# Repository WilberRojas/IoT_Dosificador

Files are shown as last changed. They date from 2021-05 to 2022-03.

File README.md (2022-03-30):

# Dosificador de medicamentos inteligente
Puede revisar el articulo en [Articulo.pdf](https://github.com/WilberRojas/IoT_Dosificador/blob/main/Articulo.pdf)

## 1. Comunicación IoT

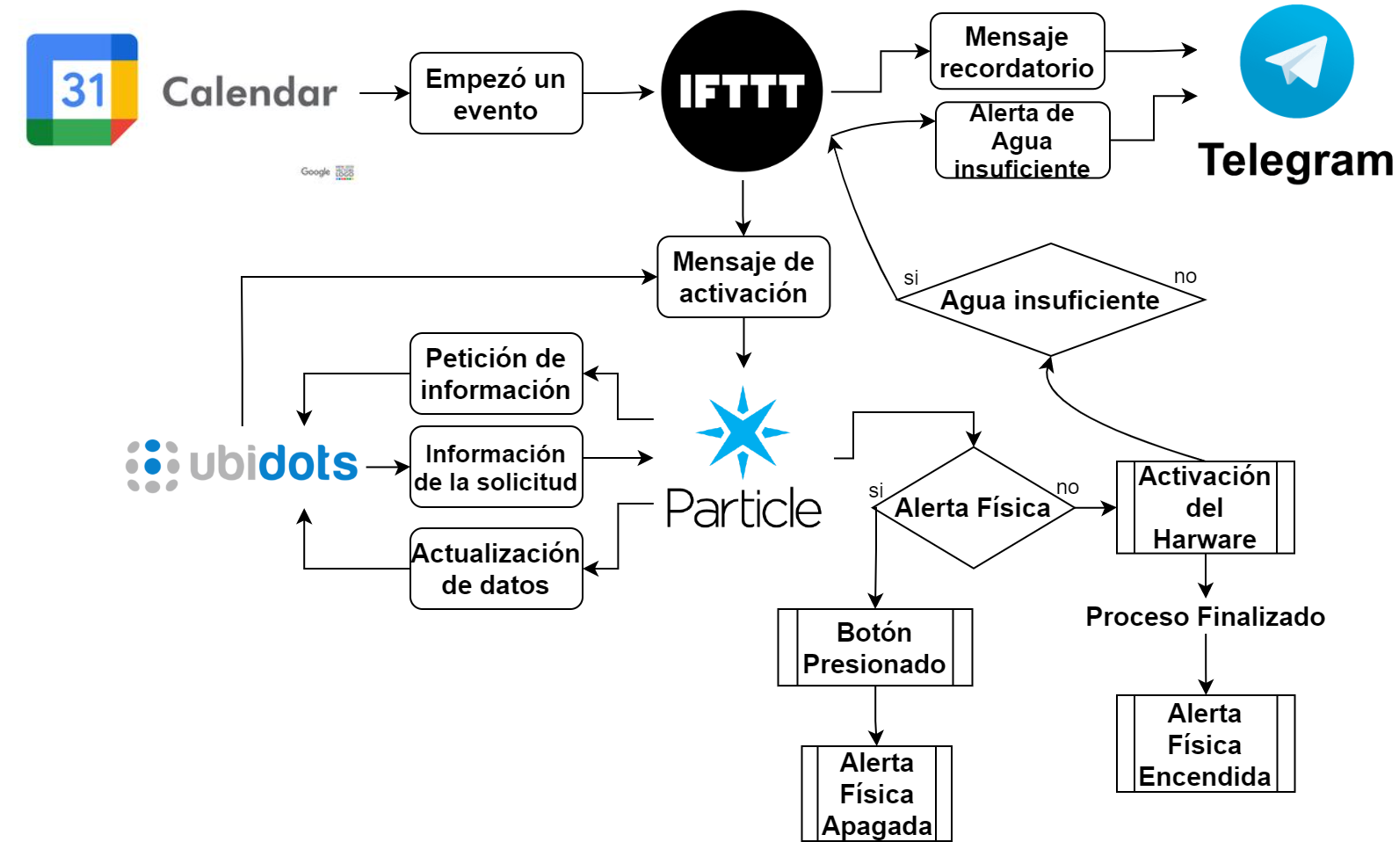
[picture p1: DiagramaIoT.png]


## 2. Prototipo en SolidWorks:

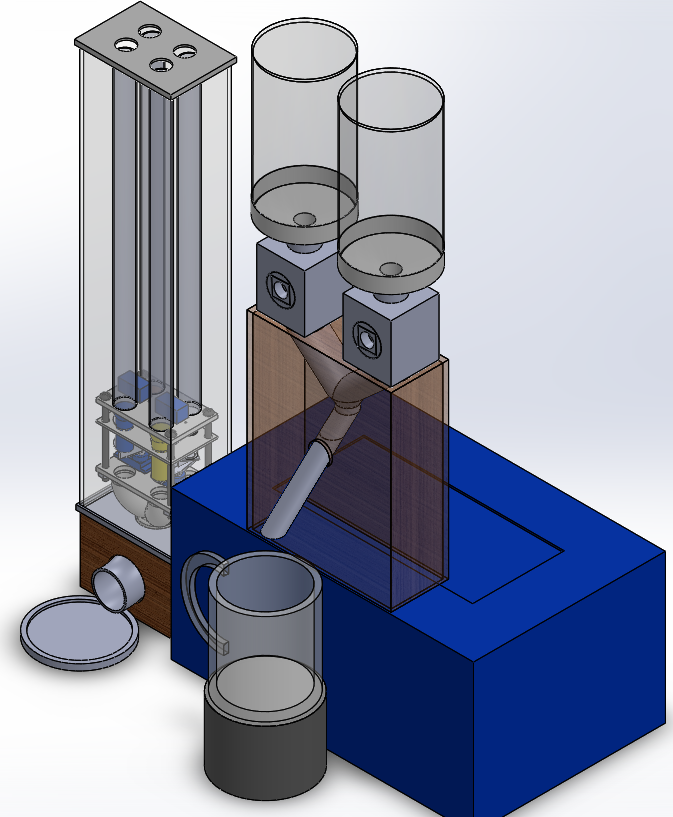
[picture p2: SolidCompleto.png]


Cada pastilla necesita un diseño personalizado en los tubos del mecanismo del dispensador

### 2.1. Mecanismo de las Pastillas

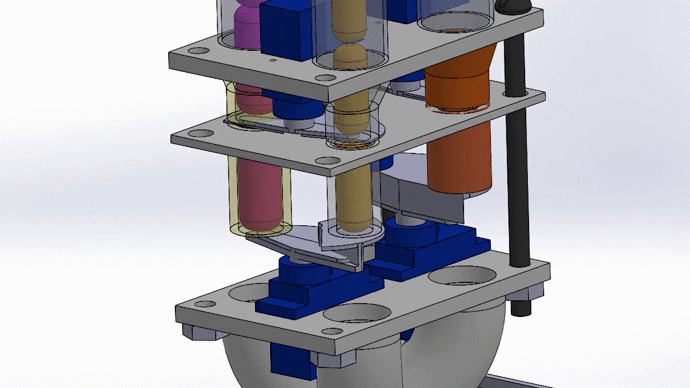
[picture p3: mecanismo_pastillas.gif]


### 2.2. Mecanismo del Azucar

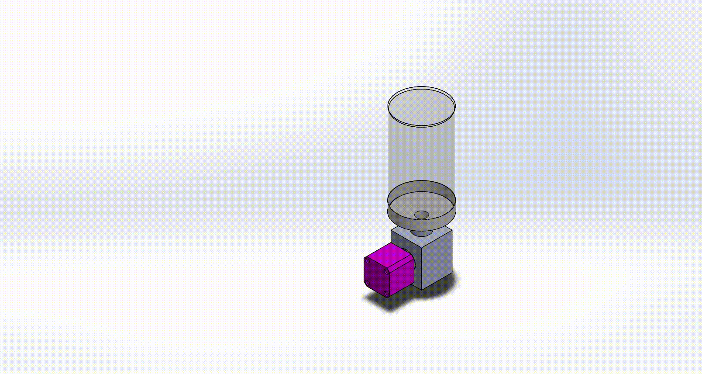
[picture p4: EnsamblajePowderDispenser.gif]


## 3. Diagrama del circuito:

Para diagramar el circuito del proyecto se uso la herramienta de https://fritzing.org/ 

Puede descargar el archivo .fzz aqui: [Diagrama_electronico.fzz](https://github.com/WilberRojas/IoT_Dosificador/blob/main/Diagrama_electronico.fzz?raw=true)

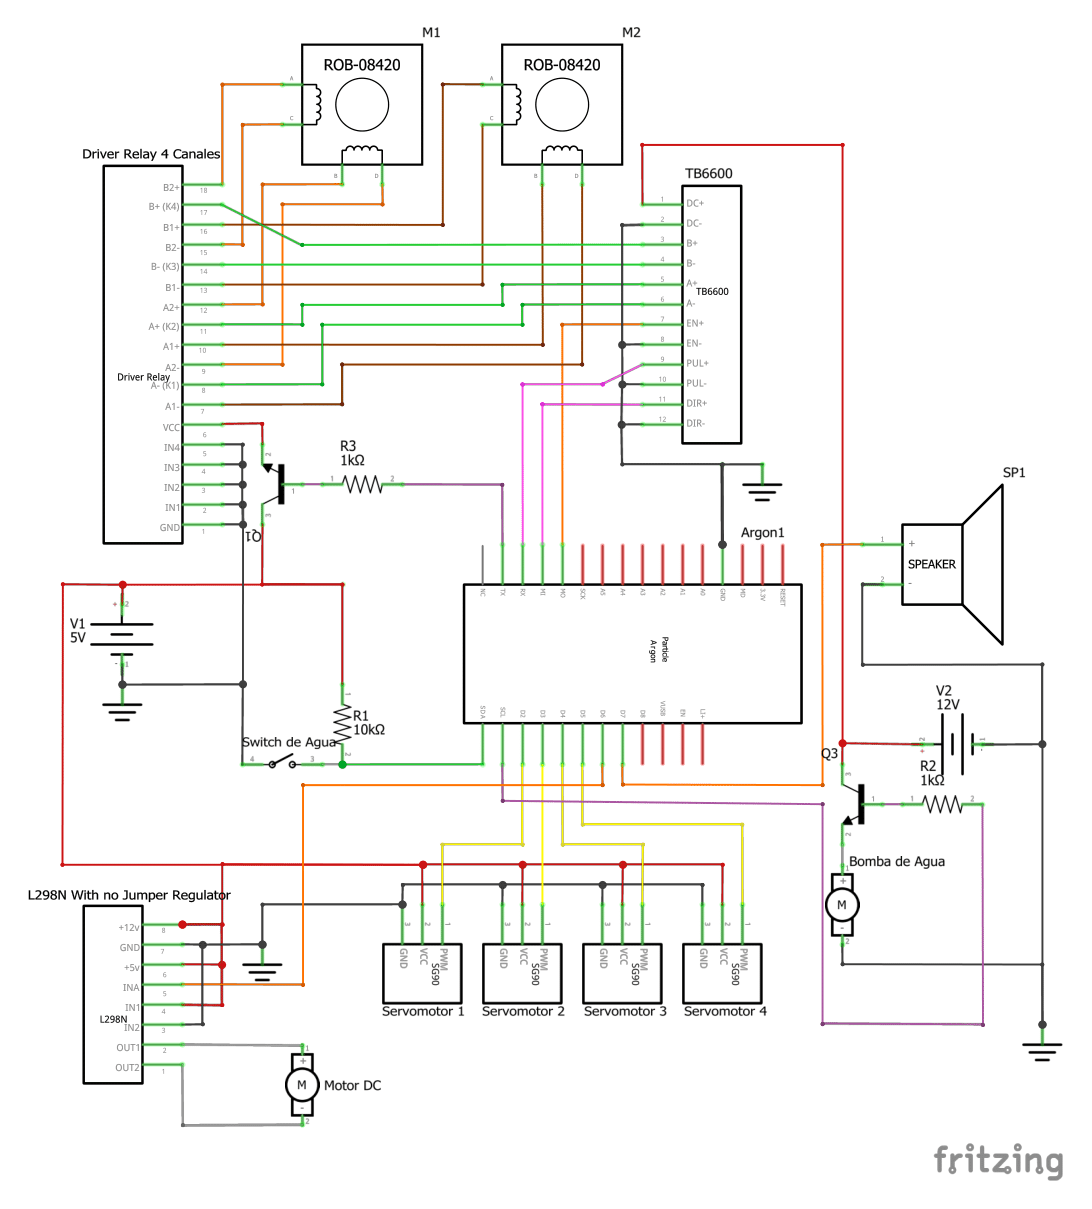
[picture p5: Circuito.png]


NOTA: Es necesario el uso de dos fuentes de alimentacion DC, no es posible alimentar el circuito solo con el VCC de salida la placa Argon debido al uso de multiples motores que requieren gran amperaje.

## 4. Codigo

#### Carpeta ```/src```:
Esta es la carpeta de origen que contiene los archivos de firmware para el proyecto. Todo lo que esté en esta carpeta se compilará en un binario de firmware para el dispositivo Particle.

#### Archivo ```.ino```:
Este archivo es el firmware que se ejecutará como la aplicación principal en el dispositivo Particle. Contiene una función `setup ()` y `loop ()`, y se puede escribir en Wiring o C / C ++. En caso de replica solo de deberá copiar el contenido de este archivo e importar las librerias dentro. Puede revisar el codigo en [stepperL298N.ino](https://github.com/WilberRojas/IoT_Dosificador/blob/main/src/stepperL298N.ino).

#### Archivo ```project.properties```:
Este es el archivo que especifica el nombre y el número de versión de las bibliotecas de las que depende el proyecto. Las dependencias se agregan automáticamente al archivo `project.properties` cuando agrega una biblioteca a un proyecto usando el comando `Particle: Install Library` en el IDE de escritorio.

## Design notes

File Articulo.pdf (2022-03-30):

# Dosificador de medicamentos inteligente

Documento para optar por el Título de Diplomado en Internet of Things Universidad Catolica Boliviana “San Pablo” Regional La Paz ´

Wilber Alvaro Rojas Fern ´ | andez ´
Estudiante del Diplomado en Internet of Things

Fabio Richard Díaz Palacios Coordinador del Diplomado en internet of Things

Resumen—Un gran numero de personas incumplen involunta- ´ riamente las dosis de su medicacion, debido a descuidos humanos. ´ Esto muchas veces repercute en la efectividad del tratamiento y recuperacion. El presente proyecto tiene como objetivo desarro- ´ llar un dispositivo dosificador inteligente para incrementar el cumplimiento de los tratamientos medicos en base a pastillas. ´ El dispositivo hace uso de Google Calendar y Ubidots para la
programacion del consumo, tambi ´ | en incluye un monitoreo de los ´
suministros, como la cantidad de pastillas o agua. El sistema propuesto se comunica con 5 servicios de internet, entre los cuales, implemento los recordatorios por Telegram. El prototipo ´ físico cuenta con la capacidad de almacenar 4 tipos de pastillas y 2 suministros solubles en agua de características arenosas o en
polvo, como el azucar. Para la explicaci ´ | on del prototipo f ´ | ísico,
se desarrollo un prototipo en Solidworks y un diagrama de ´ las conexiones del circuito. Todos los mecanismos desarrollados fueron implementados mediante el uso de la impresion 3D. Las ´ pruebas en el prototipo funcional muestran una variacion a la ´
hora de la activacion programada, retras ´ | andose hasta 10 minutos ´
de la hora exacta. Sin mas complicaciones, se concluy ´ | o que ´
el dispositivo es eficaz para ayudar en el cumplimiento de la dosificacion de pastillas. ´

Palabras clave—Dispensador, Dosificador, Medicacion, IoT, ´ Ubidots, Particle.

Línea de investigacion: ´ Ciencia, Tecnología e Innovacion, ´ Tecnologías de asistencia; desarrollo de dispositivos inteligentes aplicado a la asistencia de personas con discapacidad motora, sensorial, cognitiva.

I. INTRODUCCION´
Seguir las prescripciones de medicacion es importante ´ para obtener resultados positivos en un tratamiento. De manera mas formal, se puede referir al cumplimiento de ´ las prescripciones como la adherencia a la medicacion. La ´ falta de adherencia a la medicacion se asocia con resultados ´ adversos y mayores costos de recuperacion. No obstante, la ´ no adherencia a los medicamentos puede ser intencionada o no. El incumplimiento involuntario es un proceso en el que el paciente puede ser descuidado en el transcurso de completar el tratamiento.

La mayoría de las desviaciones en la toma de medicamentos se deben a omisiones o retrasos en la toma de dosis. Ademas, ´

Este trabajo fue entregado para su revision en fecha 21 de Mayo de ´ 2021. El autor declara que el trabajo es de su completa autoría y referencia adecuadamente otros trabajos.

los tratamientos que requieren terapia a largo plazo se han asociado con la falta de adherencia. Tambien existen otros ´ factores relacionados como la edad joven y la depresion [1]. ´

Vrijens et al. realizaron un estudio, en donde, aproximadamente la mitad de los pacientes a los que se les recetó un medicamento a largo plazo habían dejado de tomarlo en
un ano [2]. Asimismo, la mayor ˜ | ía de los pacientes tenía al
menos un período de “vacaciones de medicamentos”, esto quiere decir que hubo una falta en el cumplimiento de la
medicacion de por lo menos 3 d ´ | ías seguidos. En la imagen
1, se muestra la disminucion a lo largo del tiempo desde el ´ inicio del tratamiento, y se observa que para el día 200 el 35 % de los pacientes ya habían interrumpido el protocolo.

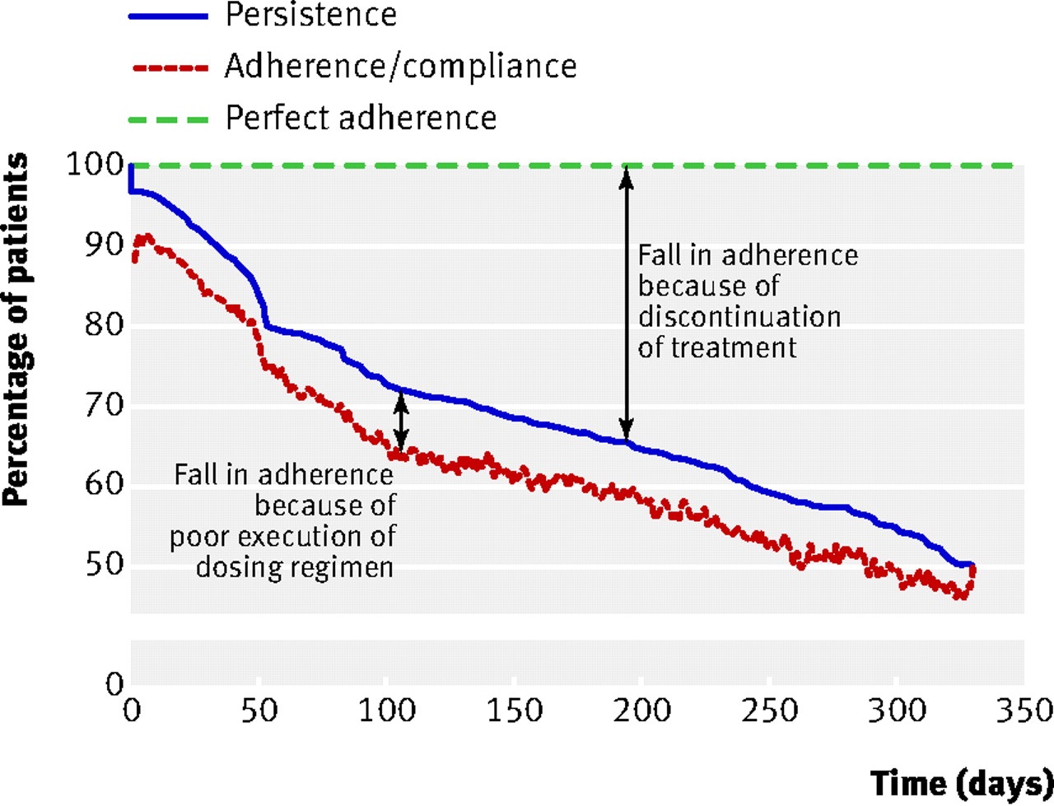
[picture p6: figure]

Figura 1. Seguimiento de la dosificacion en el transcurso de un a ´ | no [2]. ˜

Aproximadamente el 95 % de los pacientes omitieron una dosis en su tratamiento de un ano [2], es decir, tuvieron un ˜
intervalo de mas de 30 horas desde la ´ | ultima dosis tomada. De ´
acuerdo con Vrijens, la efectividad de ejecucion, repercute en ´ la efectividad de persistencia. Se puede hacer enfasis entonces, ´ en la importancia de recordar los horarios de medicacion´ para incrementar la calidad del tratamiento, por lo que en ´ este proyecto, se desarrollara un dispositivo IoT que pueda ´ ser implementado para ayudar en el cumplimiento de la
medicacion por p ´ | íldoras.

II. OBJETIVOS

A. Objetivo General
Desarrollar un dispositivo dosificador inteligente para incrementar el cumplimiento de los tratamientos medicos en base ´ a pastillas.
B. Objetivos Específicos
Implementar un sistema de control IoT.
Disenar un mecanismo capaz de dispensar m ˜ | ultiples ´
píldoras automaticamente. ´
Implementar una programacion para el horario de con- ´ sumo.
Disenar un mecanismo que otorgue complementos para ˜ el consumo bebible.
Implementar un sistema de notificacion y monitoreo. ´

III. RESULTADOS

A. Materiales
Los materiales electronicos utilizados en este proyecto se ´
los listo en la tabla I. Aparte de los listados, tambi ´ | en se us ´ | ó
la impresion 3D para la materializaci ´ | on de los mecanismos ´
disenados. ˜

Tabla I
COMPONENTES ELECTRONICOS ´
Componente | Cantidad
Particle Argon | 1
Motor DC 755 | 1
Servomotor SG90 | 4
Motor Nema 17 | 2
Bomba de agua
AD20P-1230A | 1
Driver L298N | 1
Driver TB6600 | 1
Driver Relay 4 Canales | 1
Sensor de Nivel de Agua ZPC5 | 1
Buzzer Pasivo 5v | 1
Transistor 2n2222 | 2
Resistencia 1K | 2
Resistencia 10K | 1
Fuente de 5v | 1
Fuente de 12v | 1
B. Circuito
Un diagrama completo del circuito del proyecto se puede
encontrar en el Apendice 1. En esta secci ´ | on se explicar ´ | an´
algunos puntos importantes que se tuvo en cuenta en el desarrollo.

Se implementaron 8 motores en total, por lo que se usó fuentes de voltaje externas. Se investigo la corriente necesaria ´ para el funcionamiento de los componentes, como se puede ver en la tabla II, y se calculo el amperaje requerido para ´ ambas fuentes de voltaje. Se obtuvo que la corriente necesaria para la fuente de 5v es 4.88A y para la fuente de 12v es de 4.4A.

Tabla II
AMPERAJE DE LOS COMPONENTES
Componente | Cantidad | Amperaje
Fuente de 5 voltios
Servomotor SG90 | 4 | 200mA
L298N | 1 | 4A
Driver Relay | 1 | 80mA
Fuente de 12 voltios
AD20P-1230A | 1 | 400mA
TB6600 | 1 | 4A
En el calculo, se analiz ´ | o que los dos motores Nema17 que ´
se usaron para el mecanismo del dispensador de azucar y caf ´ | é
del punto C-II, no tienen la necesidad de funcionar al mismo tiempo. Es por eso que se ha implementado un driver de reles´
de 4 canales, el cual cambiar ´ | a las salidas A+, A-, B+ y B- del ´
driver TB6600. Esto incrementa la corriente necesaria de la primera fuente 80mA, pero al usar un driver para dos motores, disminuye la corriente requerida en la segunda fuente 4A. Por otra parte, se implemento transistores como switchs ´ para la activacion de algunos componentes. En la primera ´
version del circuito, se plante ´ | o esta funci ´ | on de activaci ´ | on´
mediante el uso de reles, sin embargo, la corriente necesaria ´ para el accionamiento de un rele de 3v supera a lo que los ´ pines digitales de la placa Argon pueden otorgar. Finalmente, tomando en cuenta los datos de la tabla II , y que la corriente de funcionamiento de la Placa Argon es de 500mA a 5v, la potencia requerida para el funcionamiento del dispositivo es de:
| P = V ∗ I | | (1)

P = 5V ∗ (4,88A + 0,5A) + 12V ∗ 4,4A

| P = 79,7[W]
Se podría calcular tambien el consumo energ ´ | etico diario del ´
dispositivo, suponiendo que este encendido las 24 horas.
| E = P ∗ t | | (2)

E =

79,7 ∗ 24
1000

= 1,91[kW h]

C. Mecanismos
Se desarrollaron dos mecanismos para este proyecto: el
dispensador de pastillas, y el dispensador de azucar y caf ´ | e.´
Para su desarrollo en este proyecto, tambien se elaboraron ´ los mecanismos en Solidworks. Finalmente, se puede hacer una revision del prototipo real en el Anexo 3. ´

C-I. Dispensador de pastillas: La idea del mecanismo del dispensador de pastillas se obtuvo del proyecto de Gursimran [3]. Se usa dos servomotores para controlar la salida de las pastillas, como se observa en la figura 2. A pesar de la simplicidad de este mecanismo, se ha concluido que es uno de
los mas eficientes al momento de automatizar la dosificaci ´ | | | on. ´
Las alternativas a esta solucion implementan una rosca ´ dividida en secciones [4]. El problema con la solucion´ alternativa es que su almacenamiento es mas limitado, por ´

lo que tiene ser recargado con mas frecuencia. Adem ´ | as, ´
su organizacion se basa en el horario del consumo de las ´ pastillas, al contrario del dispensador disenado, en donde la ˜ organizacion se basa en el tipo de pastilla, sin importar el ´ horario. Finalmente, para evitar utilizar una gran cantidad de salidas PWM de la placa Argon, se disenõ un mecanismo que ´ utiliza los mismos dos servomotores para controlar la salida de 2 pastillas, esto se puede observar en el Apendice 2. ´

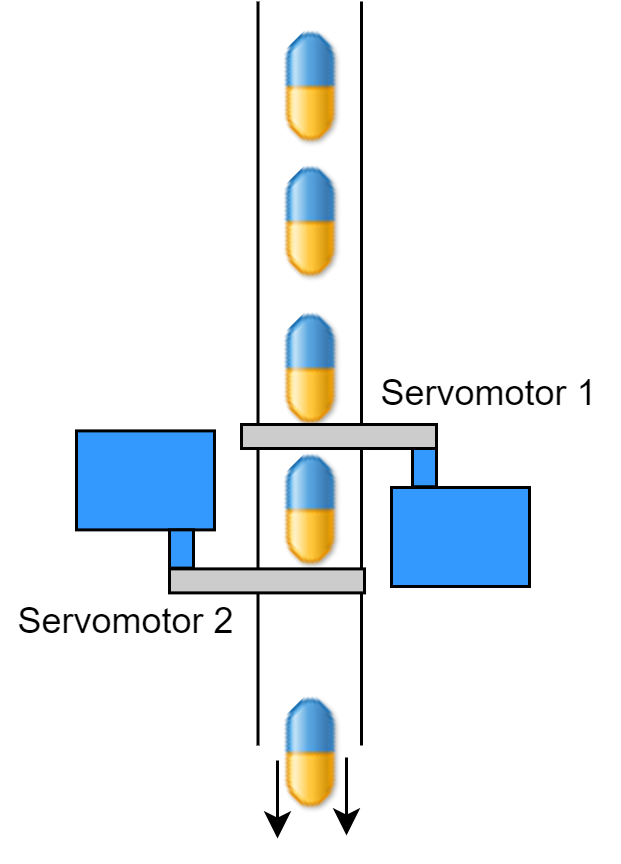
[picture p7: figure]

Figura 2. Esquema del mecanismo dispensador de pastillas.

C-II. Dispensador de azucar y caf ´ | e:´ | La base para el
diseno del dispensador de az ˜ | ucar se obtuvo de la empresa ´
de Polonia “Kazak” [5]. Se lo modifico para que su ac- ´
cionamiento sea electronico, mediante la implementaci ´ | | on de ´
un motor a pasos. Para adicionar un suministro de cafe se ´
disenõ una uni ´ | on por medio de tubos en la salida de estos ´
mecanismos, esto se puede observar mejor en el Apendice 2. ´ El funcionamiento completo de esta implementacion hace uso ´ del AD20P-1230A para adicionar agua al vaso del usuario, para luego ser mesclado por medio del batidor magnetico ´ accionado por el motor DC. La referencia para el diseno del ˜ batidor magnetico se obtuvo de Instructables [6]. ´

IV. IMPLEMENTACION´ IOT

El sistema IoT del proyecto se compone de una conexion en- ´ tre 5 servicios: Ubidots, Particle, IFTTT, Calendar y Telegram.
Se explicara la implementaci ´ | on en cada uno de estos servicios ´
en los siguientes puntos. Un diagrama de esta implementacion´ se puede ver en el apendice 1.
A. Ubidots
El servicio Ubidots permite ser usado como base de datos para las variables del sistema, almacena la informacion´
historicamente y genera una gr ´ | afica independiende para cada ´
variable, como se ve en la figura 3. Con el uso de la librería
de Particle es posible que la placa Argon almacene y recuper ´ | é
datos de este servicio.
Ubidots permite tambien la creaci ´ | on de Dashboards, en ´
donde se pueden anadir indicadores, tablas, interruptores, ˜

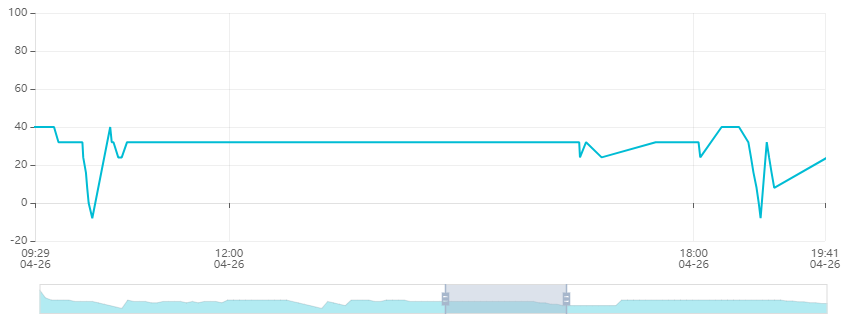
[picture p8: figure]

Figura 3. Grafico de una variable de Ubidots. ´

sliders, etc. Todos los ítems mencionados sirven para interactuar de manera mas sencilla con las variables del ´ sistema. En lo que respecta a este trabajo, los Dashboards
se usaron para hacer una simulacion de una aplicaci ´ | on ideal ´
para el proyecto.
Se dividio la implementaci ´ | on del servicio de Ubidots en ´
dos secciones para la interaccion con el usuario, una secci ´ | on´
de pedido y una seccion de datos. As ´ | í mismo, la seccion de ´
pedido esta compuesta de 3 partes o subsecciones: ´

Subseccion de pastillas ´

En esta subseccion se selecciona qu ´ | e pastillas el usuario ´
quiere tomar mediante el uso de switchs digitales, como se ve en la figura 4.

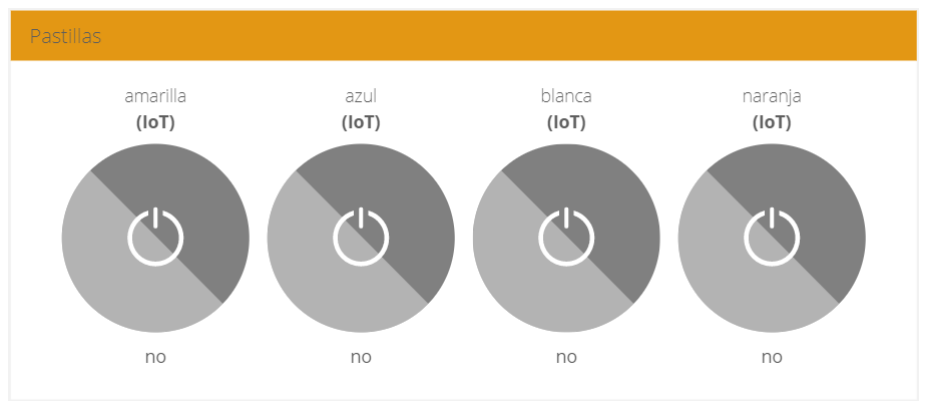
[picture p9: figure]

Figura 4. Seleccion de pastillas. ´

Subseccion de bebidas ´

La primera version implemento switches como en el caso ´ anterior, en donde el usuario podría pedir un valor entre sí o no, sin embargo, esto sería suponer que todos los usuarios consumen sus pastillas con la misma cantidad
de agua, cafe y az ´ | ucar. La implementaci ´ | on de sliders en ´
el dashboard de Ubidots se uso para cambiar el estado de ´ las variables a valores no binarios, permitiendo así una mejor personalizacion en los requerimientos del usuario, ´ como se ve en la figura 5.
Subseccion de envi ´ | ó

Se implemento un switch que al cambiar de estado en ´
sentido RISING mandara una se ´ | nal de activaci ˜ | on al ´
servidor de Particle. Idealmente este componente digital debería ser un boton, sin embargo, Ubidots actualmente ´

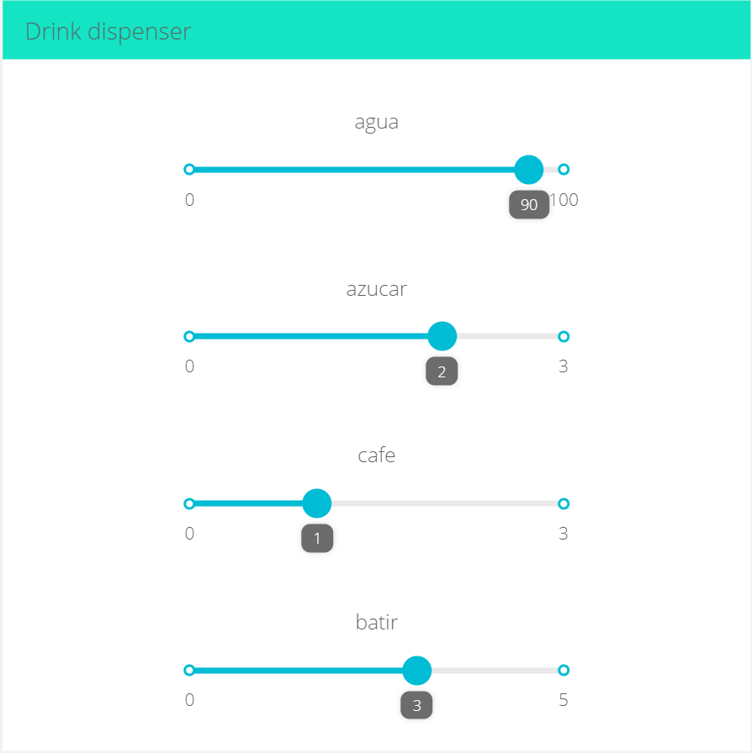
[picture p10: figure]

Figura 5. Seleccion de bebida. ´

no tiene programado un boton para su implementaci ´ | on´
en los Dashboards.
Por otro lado, la seccion de datos est ´ | a compuesta por una ´
tabla que contiene la cantidad y la hora en la que se consumió por ultima vez cada pastilla. ´

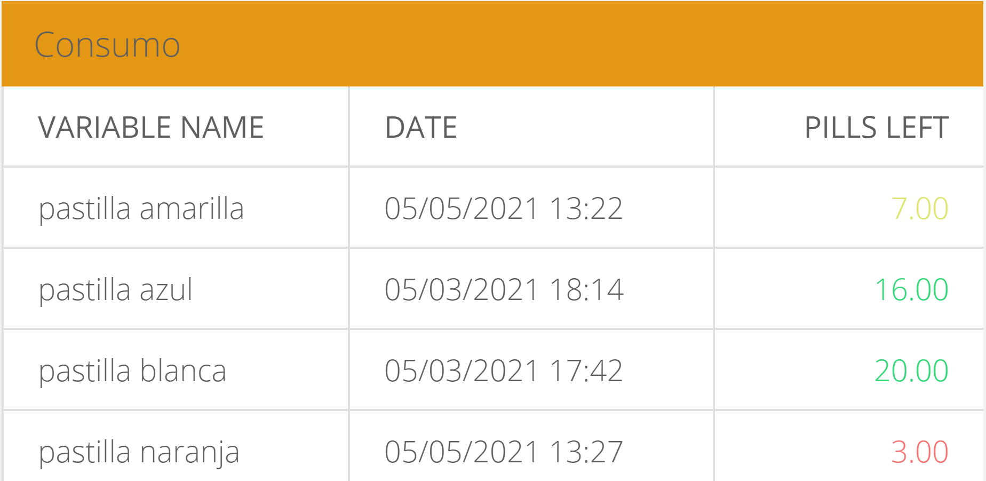
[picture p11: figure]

Figura 6. Consumo de las pastillas.

Ademas, contiene indicadores que muestran el porcentaje ´
de agua, azucar y caf ´ | e que el dispositivo f ´ | ísico almacena en
ese momento.
B. Particle
El servidor de Particle hace posible la interaccion entre ´ servicios IoT y hardware. Recibe los mensajes enviados por Ubidots y IFTTT, como se ve en la figura 7 y 8. Luego de procesar la parte del hardware en base a la solicitud recibida, envía un mensaje a Ubidots para actualizar los datos de la figura 6. Ademas, Ubidots responde si los datos han sido ´ recibidos correctamente.
C. IFTTT, Google Calendar y Telegram
IFTTT es un servicio que permite automatizar la interaccion entre otros servicios de internet. En este proyecto se ´
implemento Google Calendar para la programaci ´ | | on de los ´
horarios en los que se consumira el medicamento. Cuando ´

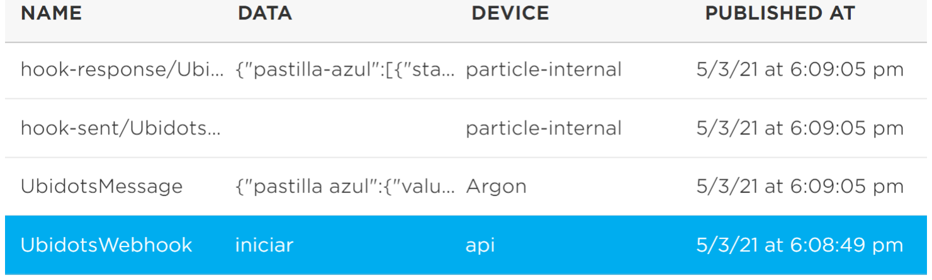
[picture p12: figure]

Figura 7. Mensaje de Inicio de Ubidots.

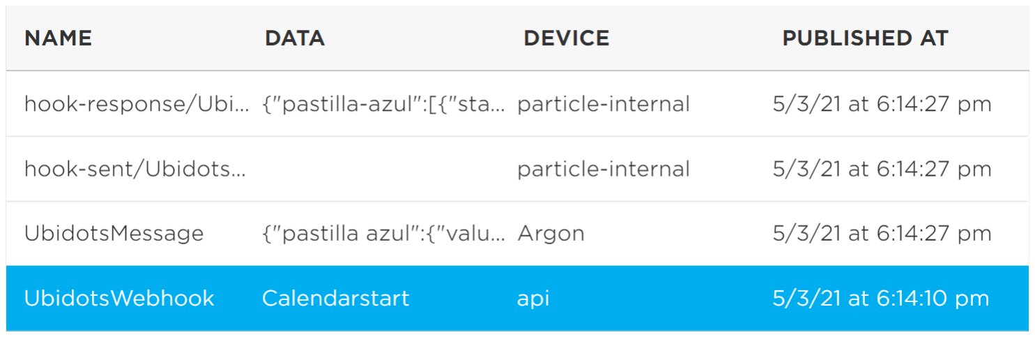
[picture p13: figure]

Figura 8. Mensaje de Inicio de IFTTT.

un evento llamado “pill” inicia, IFTTT manda un mensaje de activacion al servidor de Particle, esto es equivalente a accionar ´ el switch de enviar de la aplicacion de Ubidots. Asimismo, se ´ implemento las notificaciones por Telegram, asegurando que ´ los usuarios reciban un recordatorio a la hora de tomar sus pastillas.

V. RECOMENDACIONES

Para su replicabilidad, en el mecanismo de pastillas se re-
comienda elaborar un diseno personalizado para cada p ˜ | íldora,
debido a que, si el tubo contenedor tiene un diametro interior ´
muy elevado en comparacion al di ´ | ametro de la p ´ | íldora, puede
provocar un atascamiento por un mal asentamiento de las píldoras en cola. Por otro lado, el mecanismo del dispensador
de azucar es replicable para a ´ | nadir m ˜ | as complementos simila- ´
res, para ello se necesitara la implementaci ´ | on de m ´ | as motores a ´
paso, se sugiere utilizar un conjunto de reles para intercambiar ´ la salida del driver controlador, con el objetivo de hacer uso de un solo componente y disminuir el consumo energetico. ´ Finalmente, se recomienda una comunicacion directa entre la ´ placa Argon y Telegram, debido a que el servicio de IFTTT ´ presenta retrasos al momento de activar algunos eventos.

VI. CONCLUSIONES

Se ha desarrollado un dispositivo que cuenta con dos mecanismos principales: El dispensador de pastillas, en donde
su almacenamiento depende del tamano de cada p ˜ | íldora. El
dispensador de azucar y caf ´ | e, que junto con el funcionamiento ´
de la bomba de agua y el batidor magnetico permite una ´ solucion m ´ as completa para los usuarios. Por parte de la ´ implementacion IoT, se ha desarrollado un sistema capaz de ´ solicitar al dispositivo las pastillas y el complemento bebible
por medio de la aplicacion de Ubidots, con la opci ´ | on de ´
programar los pedidos en el servicio de Google Calendar.
Ademas, en el servicio de Ubidots tambi ´ | en se ha desarrollado ´
un monitoreo de las variables mas importantes del sistema. ´

Asimismo, se implemento recordatorios de los eventos pro- ´ gramados a Telegram. Respecto a las pruebas del prototipo funcional, se ha podido notar que para el mecanismo de las pastillas se requiere un diseno personalizado para cada ˜ píldora. Por otra parte, la activacion del sistema por medio ´ de las programaciones en Google Calendar tienden a variar,
adelantandose 2 minutos o retras ´ | andose hasta 10 minutos en ´
las pruebas. Segun la investigaci ´ | on previa, este retraso no es ´
capaz afectar la efectividad de un tratamiento, por lo que se
considera que el prototipo es valido para un desarrollo m ´ | as´
formal.

APENDICES ´

Los siguientes apendices se encuentran en el mismo repo- ´ sitorio de Github, para una mejor revision se ha separado los ´ puntos de interes en los siguientes enlaces: ´
1. Diagrama del circuito:
https://github.com/WilberRojas/IoT Dosificador/blob/ main/Circuito.md (https://github.com/WilberRojas/IoT_Dosificador/blob/main/Circuito.md)
2. Mecanismos:
https://github.com/WilberRojas/IoT Dosificador/blob/ main/mecanismos.md (https://github.com/WilberRojas/IoT_Dosificador/blob/main/mecanismos.md)
3. Prototipo Funcional:
https://github.com/WilberRojas/IoT Dosificador/blob/ main/prototipo.md (https://github.com/WilberRojas/IoT_Dosificador/blob/main/prototipo.md)
4. Codigo desarrollado para la placa Argon: ´ https://github.com/WilberRojas/IoT Dosificador/blob/ main/src/stepperL298N.ino (https://github.com/WilberRojas/IoT_Dosificador/blob/main/src/stepperL298N.ino)

Dashboards de Ubidots:
5. Pedido:
https://industrial.ubidots.com/app/dashboards/public/dashboard/qjiZKvvSNUD0r489xztf1Z11zDqJjdyEKZhmq-uRaM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 (https://industrial.ubidots.com/app/dashboards/public/dashboard/qjiZKvvSN_UD0r489xztf1Z11zDqJjdyEKZhmq-uRaM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)
6. Datos:
https://industrial.ubidots.com/app/dashboards/public/dashboard/F6vTkCbCQBkJ2pRupIU9-EW1M6ufowQUOtWs-vJPUw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 (https://industrial.ubidots.com/app/dashboards/public/dashboard/F6vTkCbCQBkJ2pRupIU9-EW1M6_ufowQUOtWs-vJPUw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)

REFERENCIAS

[1] P. Michael, C. Bryson, and J. S. Rumsfeld, “Medication adherence,” Circulation, vol. 119, 6 2009.
[2] B. Vrijens, G. Vincze, P. Kristanto, J. Urquhart, and M. Burnier, “Adherence to prescribed antihypertensive drug treatments: longitudinal study of electronically compiled dosing histories,” BMJ, vol. 336, 5 2008.
[3] G. Singh, “Iot pill dispenser,” Disponible en: https://www.instructables.com/IoT-Pill-Dispenser/, 2020.
[4] LiveFine, “Dispensador automatico de pastillas,” Disponible en: ´ https://www.amazon.com/LiveFine-Automatic-Dispenser-Electronic-Medication/dp/B00FL620B0. (https://www.amazon.com/LiveFine-Automatic-Dispenser-Electronic-Medication/dp/B00FL620B0)
[5] Kazak, “Sugar dispenser,” Disponible en: https://coffe.kazak.com.pl/product/dozator-sahara/.
[6] kymyst, “Magnetic stirrer hotplate,” Disponible en: https://www.instructables.com/How-to-make-a-magnetic-stirrer-that-looks-like-a-p/.
Wilber Alvaro Rojas Fern ´ | andez ´
Estudiante de ingeniería Mecatronica ´

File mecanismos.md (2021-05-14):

### Todos los mecanismos se encuentran en la capeta [Archivos .SLDPRT](https://github.com/WilberRojas/IoT_Dosificador/tree/main/Archivos%20.SLDPRT)

## Mecanismo de las Pastillas



### Para cada pastilla se necesita un diseño personalizado en los tubos del mecanismo del dispensador
## Mecanismo del Azucar



## Prototipo en SolidWorks:



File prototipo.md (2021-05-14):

## Prototipo

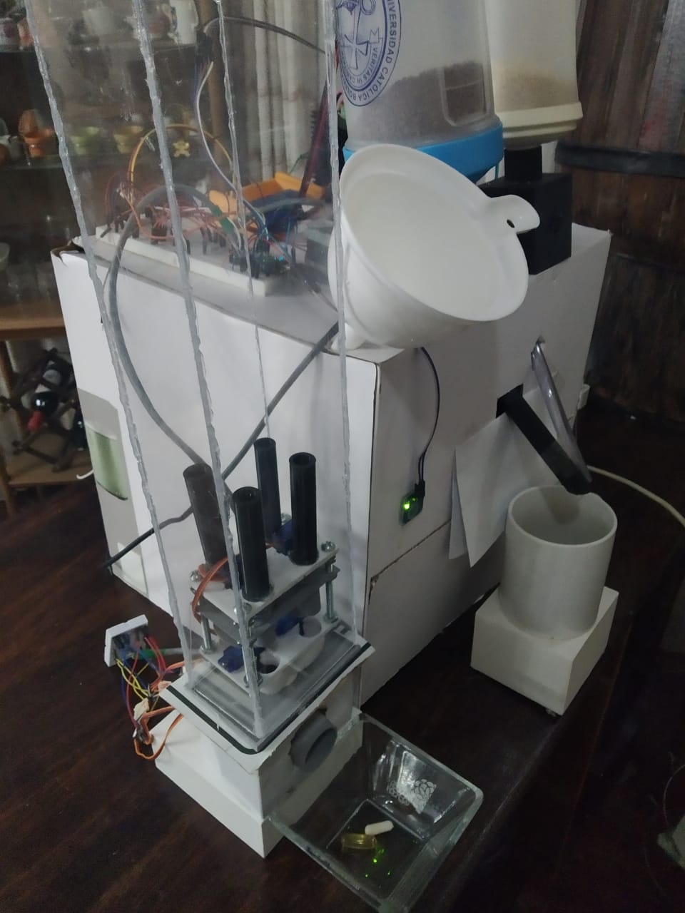
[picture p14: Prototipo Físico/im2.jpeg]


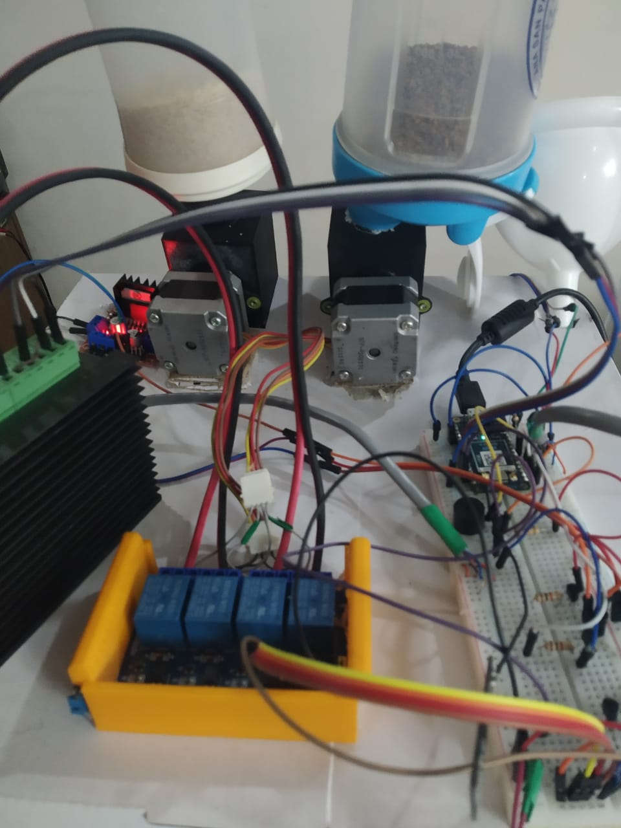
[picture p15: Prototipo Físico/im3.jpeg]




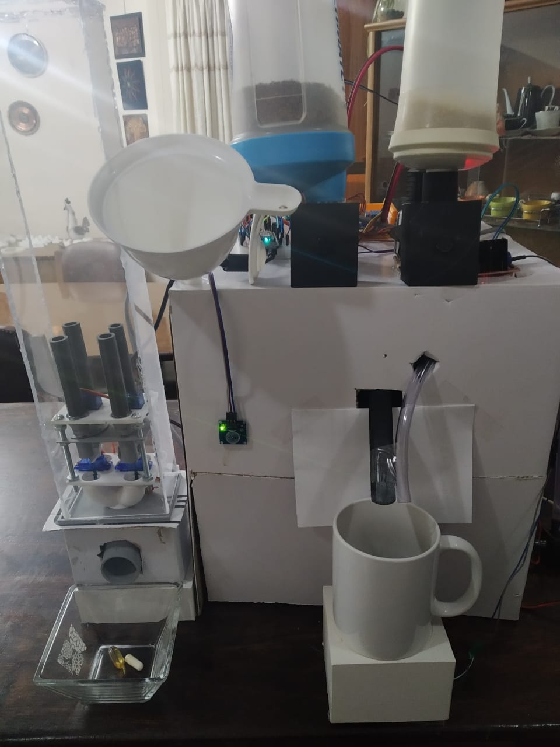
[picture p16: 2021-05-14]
Prototipo Físico/im1.jpeg

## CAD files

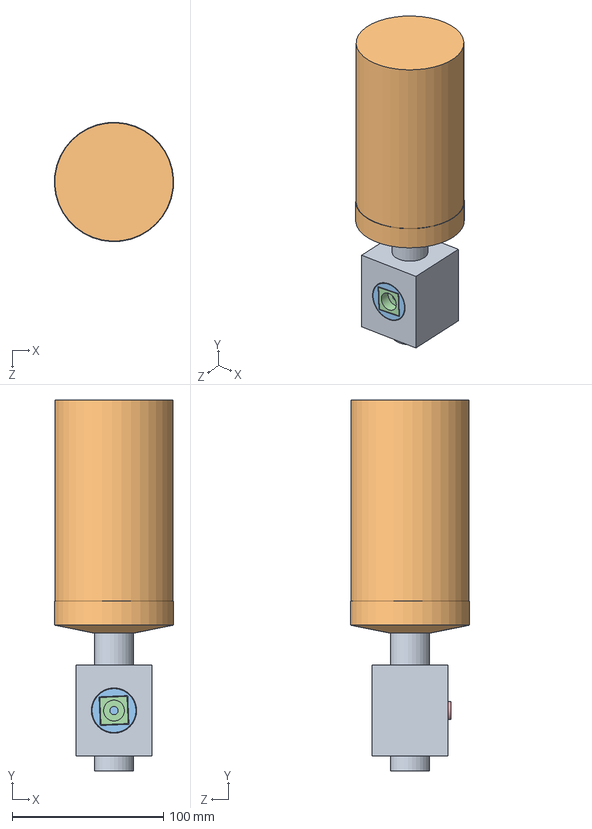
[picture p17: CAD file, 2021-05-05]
Archivos .SLDPRT/Powder Dispenser/EnsamblajePowderDispenser2.SLDASM
78.9 x 245.5 x 78.9 mm
CajaDelMedio
Botella
CilindroCentral
CuadradoTorque
EjeSoporte

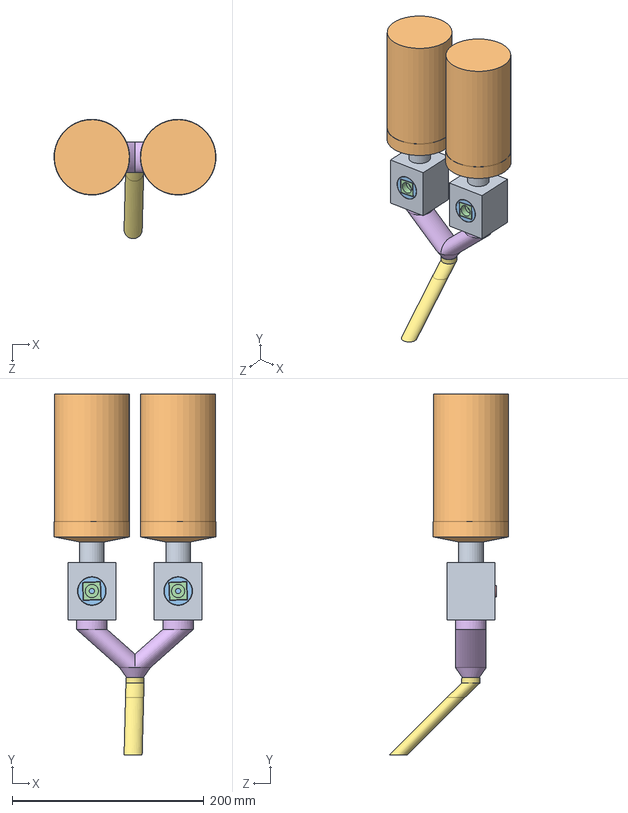
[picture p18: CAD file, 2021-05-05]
Archivos .SLDPRT/Powder Dispenser/EnsamblajePowderConEstructura.SLDASM
168.9 x 376.5 x 124.5 mm
CajaDelMedio x 2
Botella x 2
CilindroCentral x 2
CuadradoTorque x 2
EjeSoporte x 2
PowderTuboFinal1DOS
PowderTuboFinal2

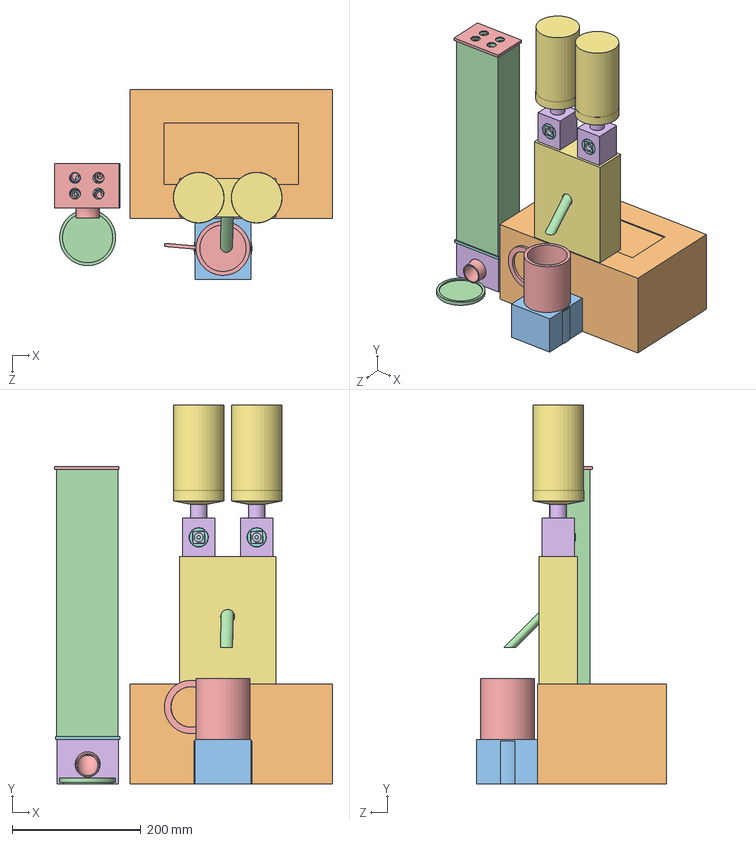
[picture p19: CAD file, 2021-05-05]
Archivos .SLDPRT/Hardware completo/EnsamblajeFinal.SLDASM
432.0 x 588.5 x 295.1 mm
ServosConTubos x 2
UnionTubos
Servo x 4
Acrilico
SoporteTubos
TubosMedio
Perno x 4
PastillaAmarrillaAjuste
PernoTuerca x 4
TuboMedioAmarrillo
TuboMedioBlanco
PastillaBlancaAjuste2
PastillaNaranjaAjuste
TuboMedioNaranja
TuboMedioAzul
PastillaAzulAjuste
BrazoServo x 4
BrazoExtension x 2
BrazoExtension_AN
BrazoExtension_AB
TapaInferiorCaja
tuboreserva x 4
TanqueDeAgua
Plato
TuboFinal
SoporteMecanismoPastillas
SoporteMecanismoPowder
SoporteMotor
Motor
SoporteImanes
TapaBatidor
BaseBatido
Taza
CajaDelMedio x 2
Botella x 2
CilindroCentral x 2
CuadradoTorque x 2
EjeSoporte x 2
PowderTuboFinal1DOS
PowderTuboFinal2

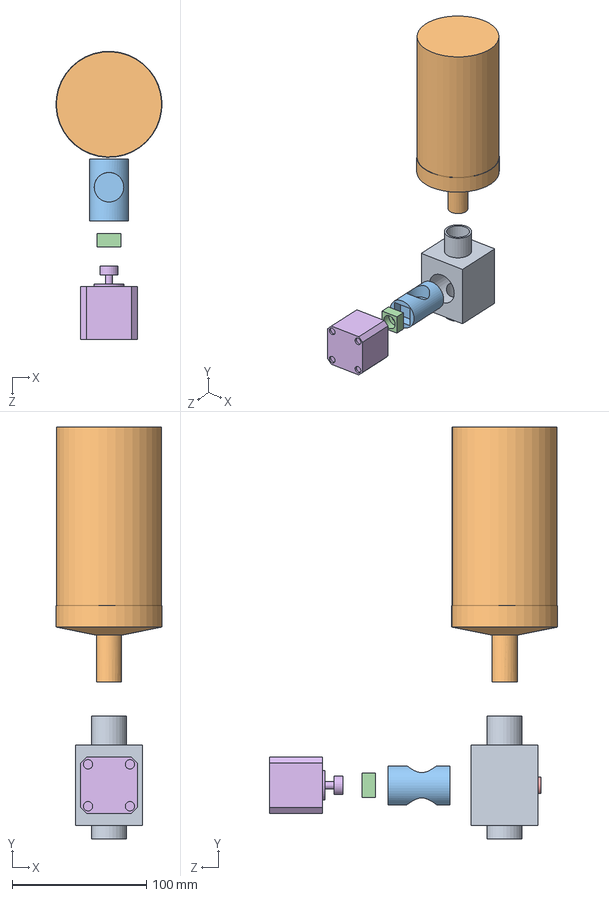
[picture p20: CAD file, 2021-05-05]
Archivos .SLDPRT/Powder Dispenser/EnsamblajePowderDispenser.SLDASM
78.9 x 306.8 x 214.7 mm
CajaDelMedio
Botella
CilindroCentral
CuadradoTorque
EjeSoporte
MotorNema

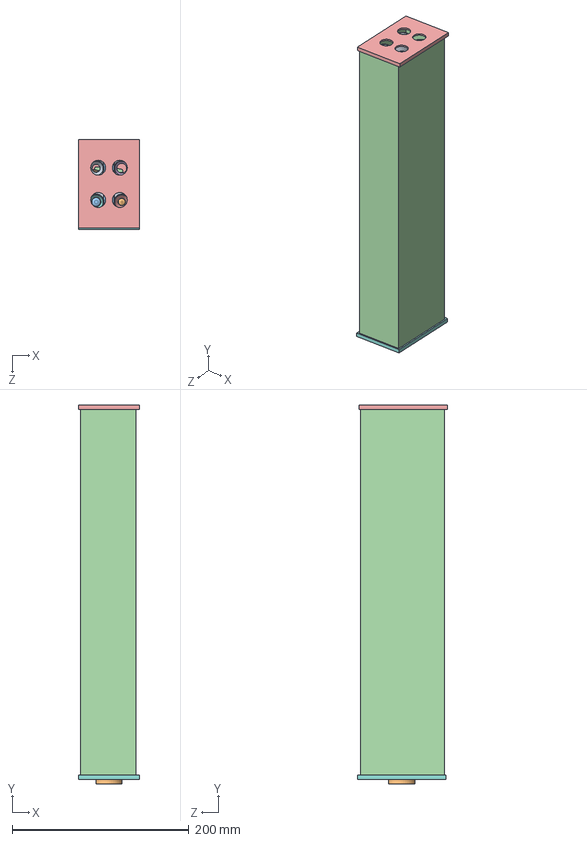
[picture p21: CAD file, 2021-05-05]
Archivos .SLDPRT/Ensamblaje1.SLDASM
68.5 x 429.0 x 102.0 mm
ServosConTubos x 2
UnionTubos
Servo x 4
SoporteTubos
TubosMedio
Perno x 2
PastillaAmarrillaAjuste
PernoTuerca x 4
TuboMedioAmarrillo
TuboMedioBlanco
PastillaBlancaAjuste2
PastillaNaranjaAjuste
TuboMedioNaranja
TuboMedioAzul
PastillaAzulAjuste
BrazoServo x 4
BrazoExtension x 2
BrazoExtension_AN
BrazoExtension_AB
TapaInferiorCaja
tuboreserva x 4
PillWhite x 4
PillOrange x 3

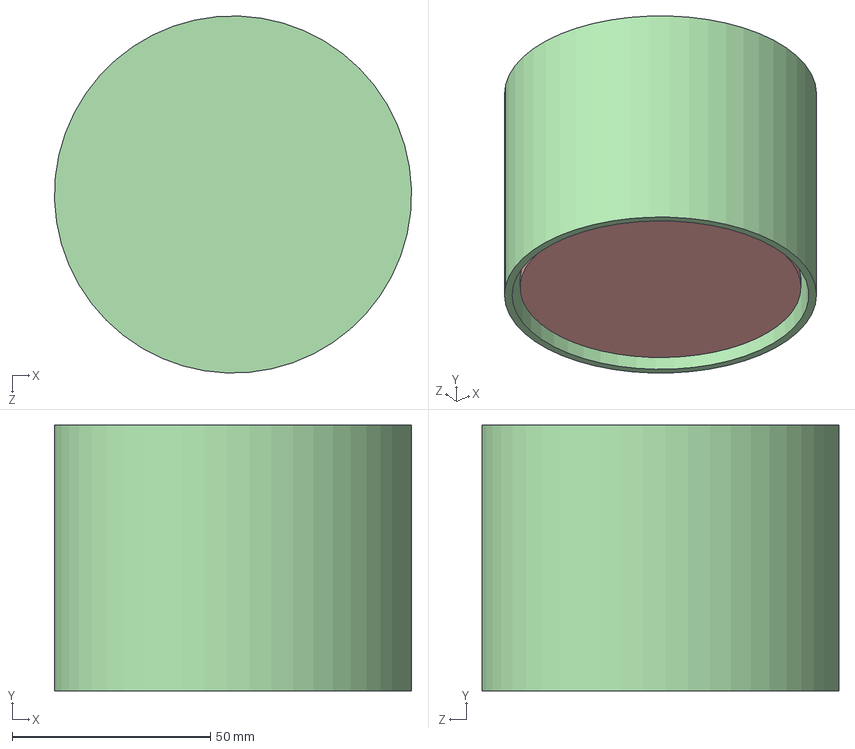
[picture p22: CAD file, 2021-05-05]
Archivos .SLDPRT/EnsamblajeBatidor.SLDASM
90.0 x 67.0 x 89.9 mm
SoporteMotor
Motor
SoporteImanes
TapaBatidor
BaseBatido

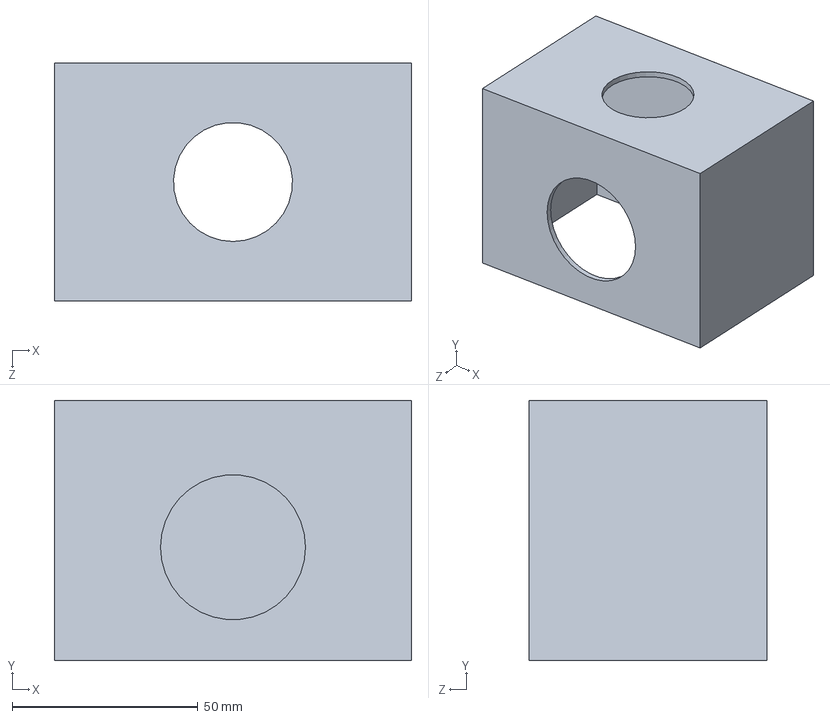
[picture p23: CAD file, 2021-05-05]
Archivos .SLDPRT/Hardware completo/SoporteMecanismoPastillas.SLDPRT
96.0 x 70.0 x 64.0 mm

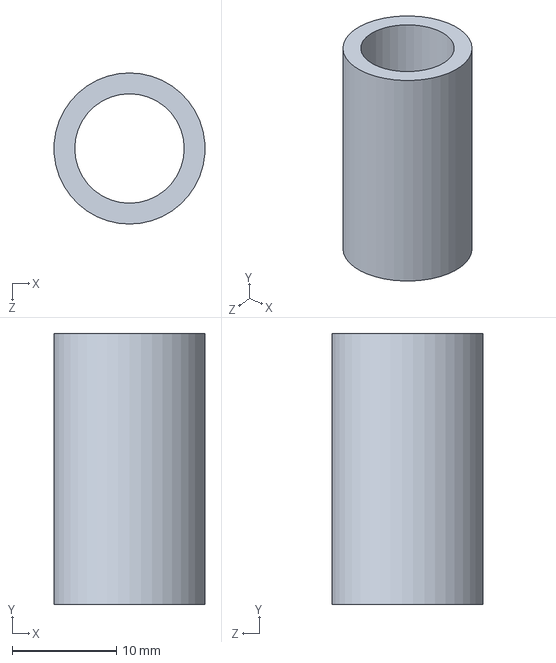
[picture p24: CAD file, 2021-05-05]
Archivos .SLDPRT/TuboMedioAmarrillo.SLDPRT
14.5 x 26.0 x 14.5 mm

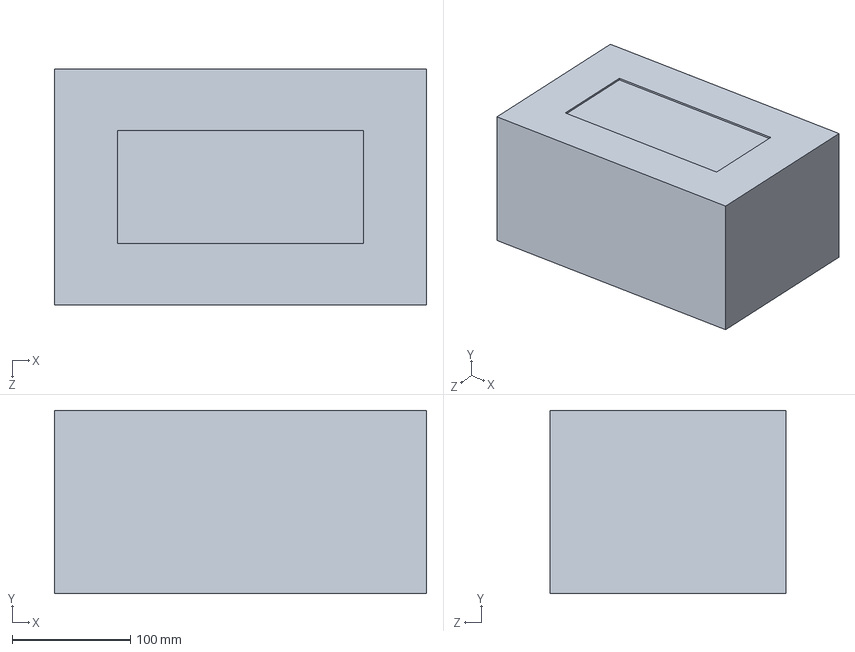
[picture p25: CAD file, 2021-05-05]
Archivos .SLDPRT/Hardware completo/TanqueDeAgua.SLDPRT
315.0 x 155.0 x 200.0 mm

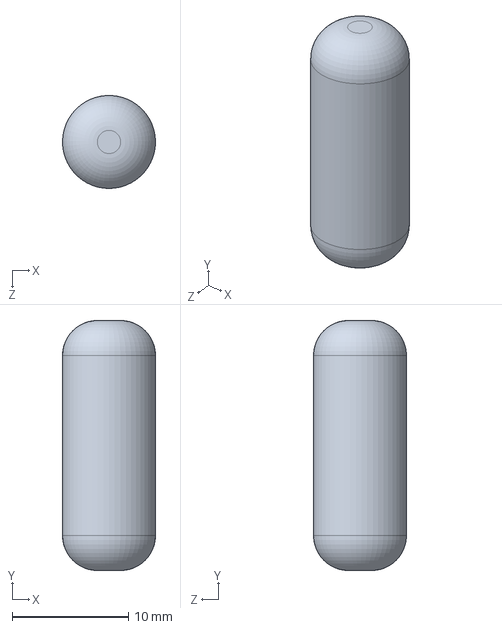
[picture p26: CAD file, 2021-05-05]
Archivos .SLDPRT/PillWhite.SLDPRT
8.00 x 21.5 x 7.99 mm

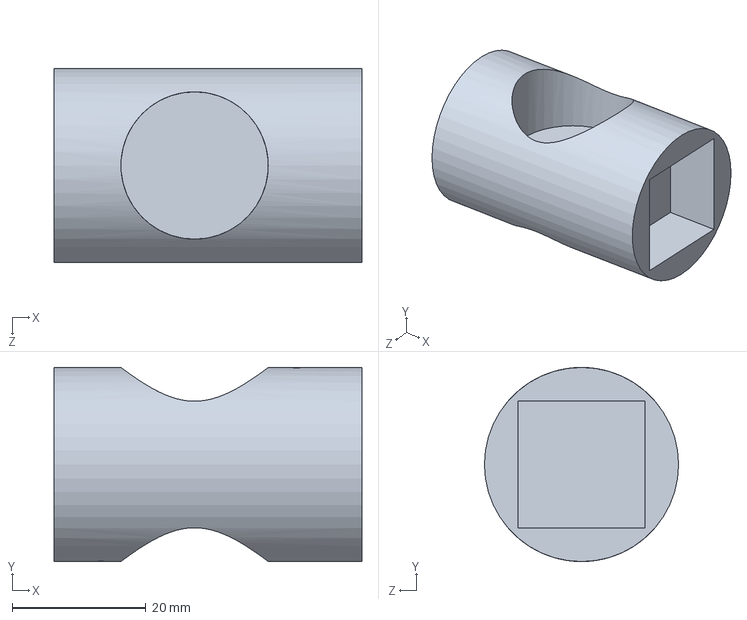
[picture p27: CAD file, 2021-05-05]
Archivos .SLDPRT/Powder Dispenser/CilindroCentral.SLDPRT
46.0 x 29.0 x 29.0 mm

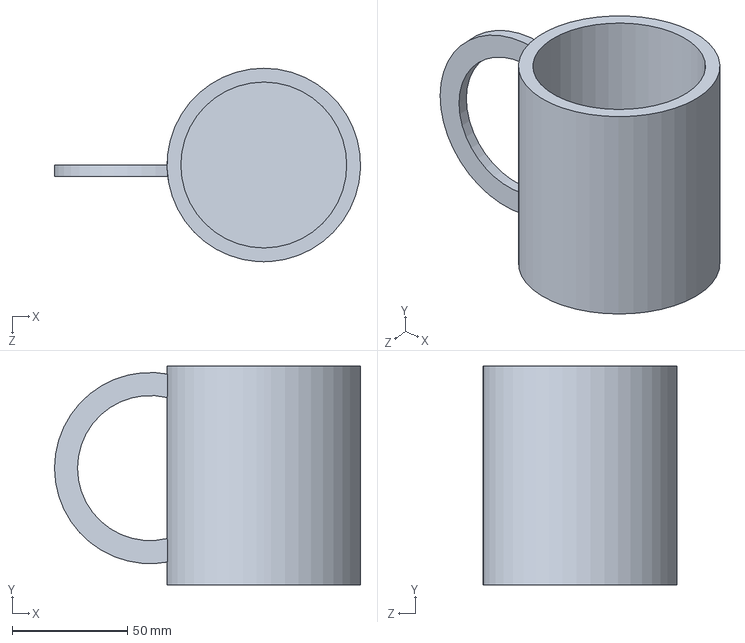
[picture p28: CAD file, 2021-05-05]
Archivos .SLDPRT/Hardware completo/Taza.SLDPRT
132.8 x 95.0 x 84.0 mm

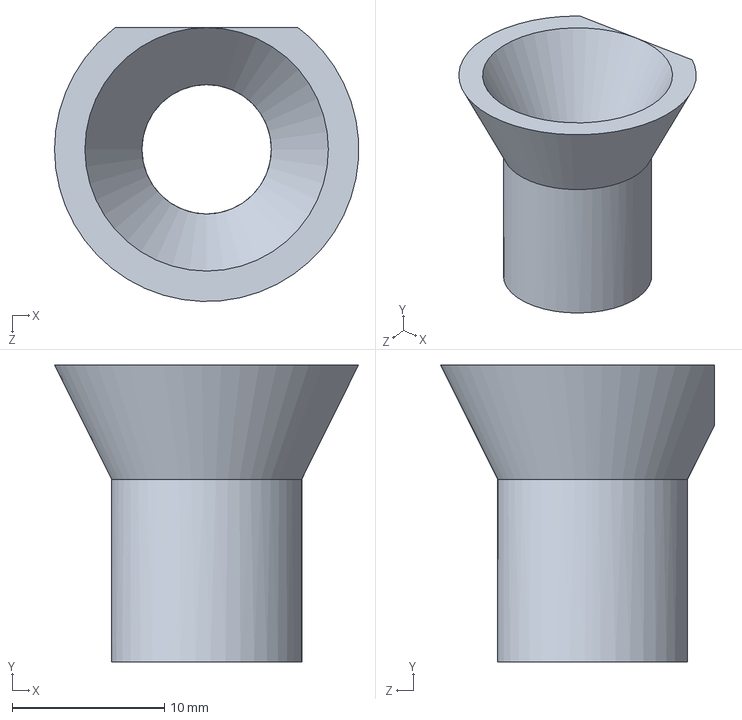
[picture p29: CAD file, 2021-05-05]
Archivos .SLDPRT/PastillaBlancaAjuste.SLDPRT
20.0 x 19.5 x 18.0 mm

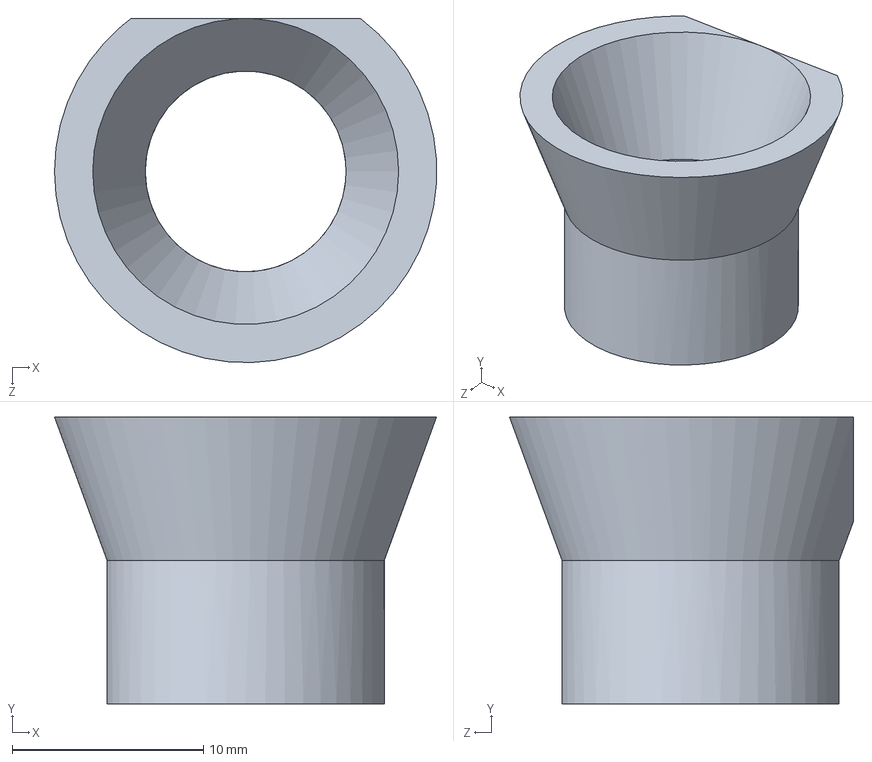
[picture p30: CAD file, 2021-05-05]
Archivos .SLDPRT/PastillaAmarrillaAjuste.SLDPRT
20.0 x 15.0 x 18.0 mm

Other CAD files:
Archivos .SLDPRT/Powder Dispenser/CajaDelMedio.SLDPRT
Archivos .SLDPRT/Acrilico.SLDPRT
Archivos .SLDPRT/Hardware completo/SoporteMecanismoPowder.SLDPRT
Archivos .SLDPRT/Powder Dispenser/EjeSoporte.SLDPRT
Archivos .SLDPRT/BaseBatido.SLDPRT
Archivos .SLDPRT/BrazoExtension.SLDPRT
Archivos .SLDPRT/BrazoExtension_AB.SLDPRT
Archivos .SLDPRT/BrazoExtension_AN.SLDPRT
Archivos .SLDPRT/BrazoServo.SLDPRT
Archivos .SLDPRT/BrazoTubo1.SLDPRT
Archivos .SLDPRT/Hardware completo/BatidorMagnetico.SLDPRT
Archivos .SLDPRT/Hardware completo/Plato.SLDPRT
Archivos .SLDPRT/Hardware completo/PowderTuboFinal1.SLDPRT
Archivos .SLDPRT/Hardware completo/PowderTuboFinal1DOS.SLDPRT
Archivos .SLDPRT/Hardware completo/PowderTuboFinal2.SLDPRT
Archivos .SLDPRT/Motor.SLDPRT
Archivos .SLDPRT/PastillaAzulAjuste.SLDPRT
Archivos .SLDPRT/PastillaAzulAjuste2.SLDPRT
Archivos .SLDPRT/PastillaBlancaAjuste2.SLDPRT
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

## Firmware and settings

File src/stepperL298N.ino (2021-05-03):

#include <Ubidots.h>
//Globals
#define SwitchWater D0
#define BombaWater D1
#define ServoBY1 D2
#define ServoBY2 D3 //**
#define ServoAN1 D4
#define ServoAN2 D5
#define DCmotor D6
#define AlarmPin D7
#define touchbutton D8
#define ChangeNema D10
#define STEPPIN D11 //pull
#define DIRPIN D12
#define ENAPIN D13

const int STEPTIME = 2; //steps delay
const char *WEBHOOK_NAME= "UbidotsMessage";       //Declaramos el webhook configurado en la consola de Particle
Ubidots ubidots("webhook", UBI_PARTICLE);
Ubidots ubidotsGET("BBFF-scd8n8yDi9om9Vxg650ESuM26GeLQ9",UBI_TCP);
//variables
boolean iniciar = false;
boolean switchStatus = false;
boolean pill_blue = false;
boolean pill_white = false;
boolean pill_orange = false;
boolean pill_yellow = false;
int water_var = 0;
int sugar_teaspoons = 0;
int coffee_teaspoons = 0;
bool batir=false;
//const delays
const int t1servos=2000;
const int t2servos=500;
const int twater=6000;
const int tchangenema=2000;
const int tbatir=60000;
//-----------------------------
float batir_variable=0.0;
boolean reminderAlarm=false;
//VALORES INICIALES
int nivelagua = 40;
int nivelcafe = 30;
int nivelazucar = 50;
int cantazul = 20;
int cantamarillo = 20;
int cantblanco =  20;
int cantnaranja = 20;
//update
bool upblue=false;
bool upyellow=false;
bool uporange=false;
bool upwhite=false;
bool upwater=false;
bool upcoffee=false;
bool upsugar=false;
//------------------
bool initupdate=true;
void setup(){ //----------------------------------------Setup
  //Stepper
  pinMode(STEPPIN,OUTPUT);
  pinMode(DIRPIN,OUTPUT);
  pinMode(ENAPIN,OUTPUT);
  //Servos  
  pinMode(ServoAN1,OUTPUT);
  pinMode(ServoAN2,OUTPUT);
  pinMode(ServoBY1,OUTPUT);
  pinMode(ServoBY2,OUTPUT);
  //-----
  pinMode(DCmotor,OUTPUT);
  pinMode(ChangeNema,OUTPUT);
  pinMode(SwitchWater,INPUT);
  pinMode(BombaWater,OUTPUT); 
  pinMode(AlarmPin,OUTPUT);
  pinMode(touchbutton,INPUT);
  attachInterrupt(touchbutton, interruptFunTouch, CHANGE);
  Particle.subscribe("UbidotsWebhook", UbidotsMessages);  
}

void loop() { //------------------------------------------------------------------------------Loop
  if(initupdate) updateFun();
  String mssg = "Iniciar: "+String(iniciar) + " Amarillo:"+String(pill_yellow)+" Azul:"+String(pill_blue)+" Blanco:"+String(pill_white)+" Naranja:"+String(pill_orange)+" %Agua:"+String(water_var)+" #Cafe:"+String(coffee_teaspoons)+" #Azucar:"+String(sugar_teaspoons)+" Batir:"+String(batir_variable)+" Alarm:"+String(reminderAlarm);
  Serial.println(mssg);  
  if(iniciar and !reminderAlarm){
    reminderAlarm=true;
    switchStatus=digitalRead(SwitchWater);
    if(switchStatus){
      Particle.publish("nowater", "1", PUBLIC);     
      water_var=0;
      iniciar=0;
      for(int i=0;i<6;i++){
        analogWrite(AlarmPin, 100);
        delay(300); 
        analogWrite(AlarmPin, 0);
        delay(300);
      }
    }
    if(water_var or coffee_teaspoons or sugar_teaspoons) WCSFun();
    else  if(batir_variable) batirFun();
    PillsFun();
    iniciar=false;
    updateFun();
  }
  if(reminderAlarm){
    for(int i=0;i<3;i++){
      analogWrite(AlarmPin, 150);
      delay(600); 
      analogWrite(AlarmPin, 0);
      delay(600);
    }
  }
  delay(1000);
}

void PillsFun() {//---------------------------------------------------------------------------PillsFun
  if(pill_yellow){//---------------------------------yellow
    analogWrite(ServoAN2, 50);
    delay(t1servos);
    analogWrite(ServoAN2, 130);
    delay(t2servos);
    analogWrite(ServoAN1, 70);
    delay(t1servos);
    analogWrite(ServoAN1, 130);
    delay(t2servos);
    pill_yellow=false;
    upyellow=true;
    cantamarillo--;
  }
  if(pill_blue){//---------------------------------Blue
    analogWrite(ServoBY2, 50);
    delay(t1servos);
    analogWrite(ServoBY2, 130);
    delay(t2servos);
    analogWrite(ServoBY1, 50);
    delay(t1servos);
    analogWrite(ServoBY1, 130);
    delay(t2servos);
    pill_blue=false;
    upblue=true;
    cantazul--;
  }
  if(pill_white){//---------------------------------white
    analogWrite(ServoAN2, 180);
    delay(t1servos);
    analogWrite(ServoAN2, 130);
    delay(t2servos);
    analogWrite(ServoAN1, 190);
    delay(t1servos);
    analogWrite(ServoAN1, 130);
    delay(t2servos);
    pill_white=false;
    upwhite=true;
    cantblanco--;
  }
  if(pill_orange){//---------------------------------orange
    analogWrite(ServoBY2, 170);
    delay(t1servos);
    analogWrite(ServoBY2, 130);
    delay(t2servos);
    analogWrite(ServoBY1, 220);
    delay(t1servos);
    analogWrite(ServoBY1, 130);
    delay(t2servos);
    pill_orange=false;
    uporange=true;
    cantnaranja--;    
  }
}

void WCSFun(){//------------------------------------------------------------------water+coffee+sugar  
  if(water_var>0 and !switchStatus){
    digitalWrite(BombaWater, true); //activar bomba
    nivelagua=nivelagua-5;
    upwater=true;
  } 
  digitalWrite(ChangeNema, false); //nema change
  delay((twater*water_var)/100);
  digitalWrite(BombaWater, false); //apagar bomba  

  while(sugar_teaspoons>0){ //activar azucar
    forward(200);
    sugar_teaspoons--;
    batir=true;
    nivelazucar=nivelazucar-2;
    upsugar=true;
    delay(tchangenema);    
  }
  delay(tchangenema);
  digitalWrite(ChangeNema, true); //nema change  
  delay(tchangenema);
  while(coffee_teaspoons>0){ //activar cafe
    forward(200);
    coffee_teaspoons--;
    batir=true;
    nivelcafe=nivelcafe-2;
    upcoffee=true;
    delay(tchangenema);
  }
  digitalWrite(ChangeNema, false); //nema change
  if(batir_variable){
    digitalWrite(DCmotor, 1); //activar batidor
    delay(tbatir*batir_variable);
  } 
  batir=false;
  analogWrite(DCmotor, 0); //apagar batidor
  //reset values
  water_var=0;
  sugar_teaspoons=0;
  coffee_teaspoons=0;     
}

void batirFun(){
  analogWrite(DCmotor, 250); //activar batidor
  delay(tbatir*batir_variable);
  analogWrite(DCmotor, 0);
}

void UbidotsMessages(const char *event, const char *data)//------------------------------UbidotsMessages
{
  String datastring= String(data);
  Serial.println("RECIBIENDO DATOS ..."); 
  if(datastring.equals("iniciar") or datastring.equals("Calendarstart")){
    pill_blue=(bool) ubidotsGET.get("proyecto","azul");
    pill_orange=(bool) ubidotsGET.get("proyecto","naranja");
    pill_white=(bool) ubidotsGET.get("proyecto","blanca");
    pill_yellow=(bool) ubidotsGET.get("proyecto","amarilla");
    water_var=(int) ubidotsGET.get("proyecto","agua");
    coffee_teaspoons=(int) ubidotsGET.get("proyecto","cafe");
    sugar_teaspoons=(int) ubidotsGET.get("proyecto","azucar");
    batir_variable=(float) ubidotsGET.get("proyecto","batir");
    iniciar=true;
  }
   
}

void forward(int steps){ //---------------------------------------------------------------------forward
  //400 steps 1 revolution
  int i;
  digitalWrite(ENAPIN,LOW);
  digitalWrite(DIRPIN,HIGH);//SET DIRECTION 
  for(i=0;i<steps;i++){
    digitalWrite(STEPPIN,HIGH);
    delay(STEPTIME);
    digitalWrite(STEPPIN,LOW);
    delay(STEPTIME);  
  }  
  digitalWrite(ENAPIN,HIGH);//DISABLE STEPPER
}

void updateFun(){ //----------------------------------------------------------------------update ubidots
  if(upwater or initupdate) ubidots.add("nivelagua", (float) nivelagua);
  if(upcoffee or initupdate) ubidots.add("nivelcafe", (int) nivelcafe);
  if(upsugar or initupdate) ubidots.add("nivelazucar", (int) nivelazucar);
  if(upyellow or initupdate) ubidots.add("pastilla amarilla",(float) cantamarillo);
  if(upblue or initupdate) ubidots.add("pastilla azul", (int) cantazul);
  if(upwhite or initupdate) ubidots.add("pastilla blanca", (int) cantblanco);
  if(uporange or initupdate) ubidots.add("pastilla naranja", (int) cantnaranja);
  ubidots.send(WEBHOOK_NAME, PUBLIC);
  upblue=false;
  upyellow=false;
  uporange=false;
  upwhite=false;
  upwater=false;
  upcoffee=false;
  upsugar=false;
  initupdate=false;
}

void interruptFunTouch()//funcion de interrupcion
{   
  reminderAlarm=false;
}
